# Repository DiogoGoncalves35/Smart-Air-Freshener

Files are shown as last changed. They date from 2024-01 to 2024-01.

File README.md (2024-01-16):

# Smart Air Freshner

    

This board is designed to control a standard Air Freshener via ESPHome and Home Assistant, this way it's possible to automate the device by time or any condition defined.





The board fits in the same place as the default board because both have the same dimensions.





------------

### Schematic 

The [schematic](/Hardware/PCB/Schematic.pdf) is arround ESP12-E module with the basic configuration (Resistors needed), the AMS1117 regulates the 5V input voltage to 3.3V. The microcontroller controls the motor via an 2N2222 transistor and the 1N4007 diode protects the circuit in case of back voltage generated when the motor turns off.

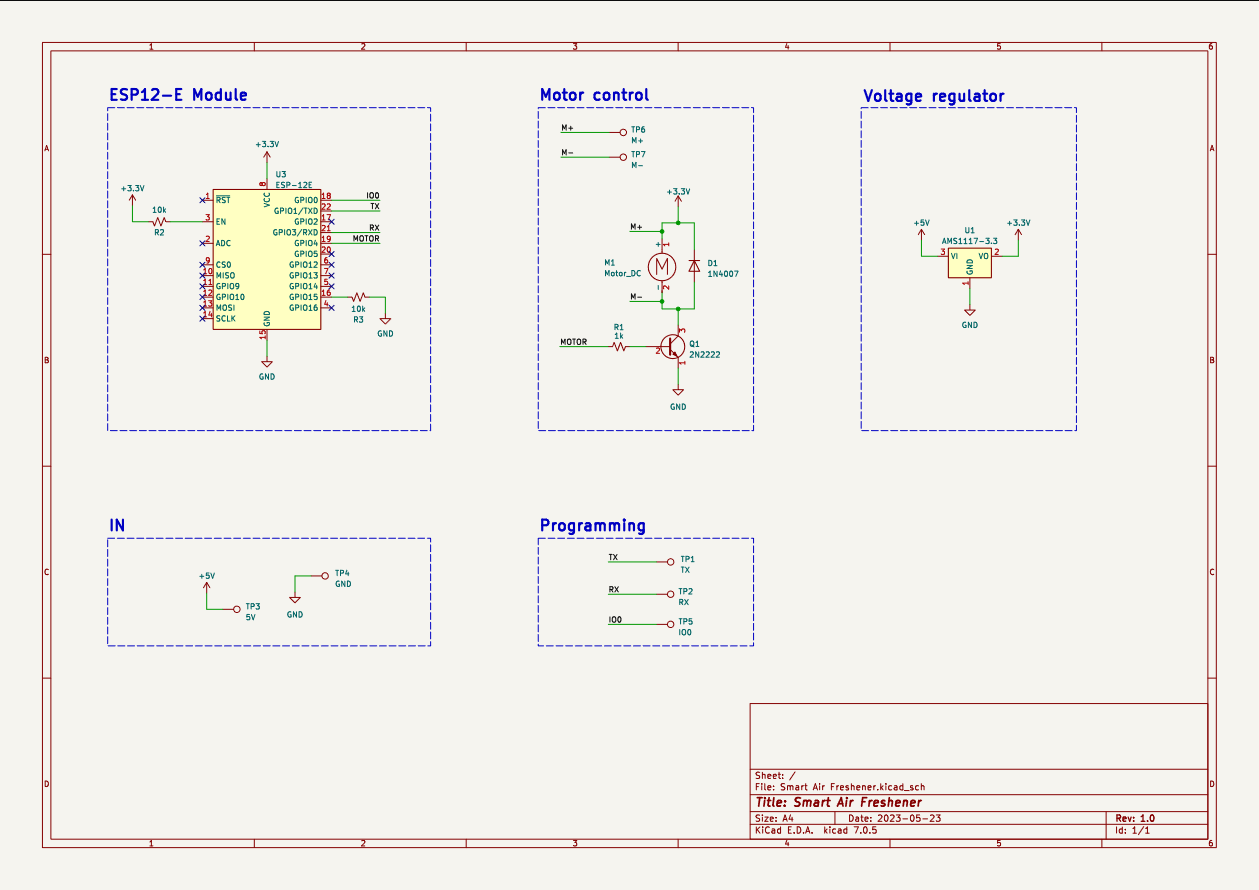
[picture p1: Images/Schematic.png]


------------

### PCB

[This](Hardware/PCB/) 1.6mm board contains 2 layers, both connected to GND, under the antenna GND area was removed. Programming connectors are SMD because it's only necessary to program the board once, after, it's possible to program over-the-air. Design it's not the best and should be improved, the only problem is related to component placement, there isn't much space to put the components on the edges.

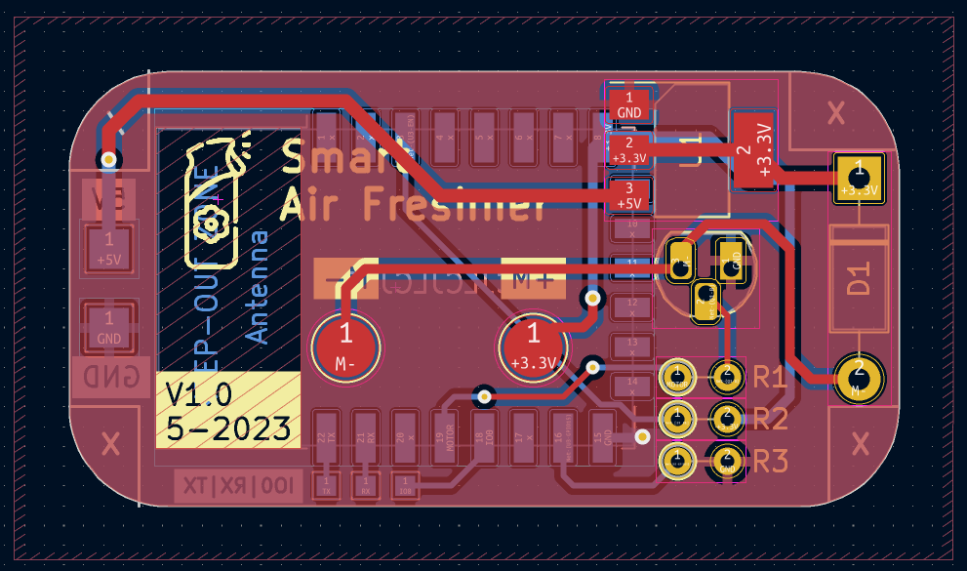
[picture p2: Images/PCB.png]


---

### ESPHome Code

This code block contains the needed code to control the air freshener. Whenever Spray button is pressed in Home Assistant, the motor turns on for a second and then turns off. With the button inside HA, it's possible to automate the device in different ways.

```
button:
  - platform: template
    name: "Spray"
    icon: "mdi:air-purifier"
    on_press:
    - switch.turn_on: motor
    - delay: 1000ms
    - switch.turn_off: motor

switch:
  - platform: gpio
    pin: GPIO4
    id: motor
```
------------

### Known issues

- None for now

------------

### To-Do

- USB-C connector ? (Better for connecting, removes need for soldering)
- Fuse protection
- SMD components

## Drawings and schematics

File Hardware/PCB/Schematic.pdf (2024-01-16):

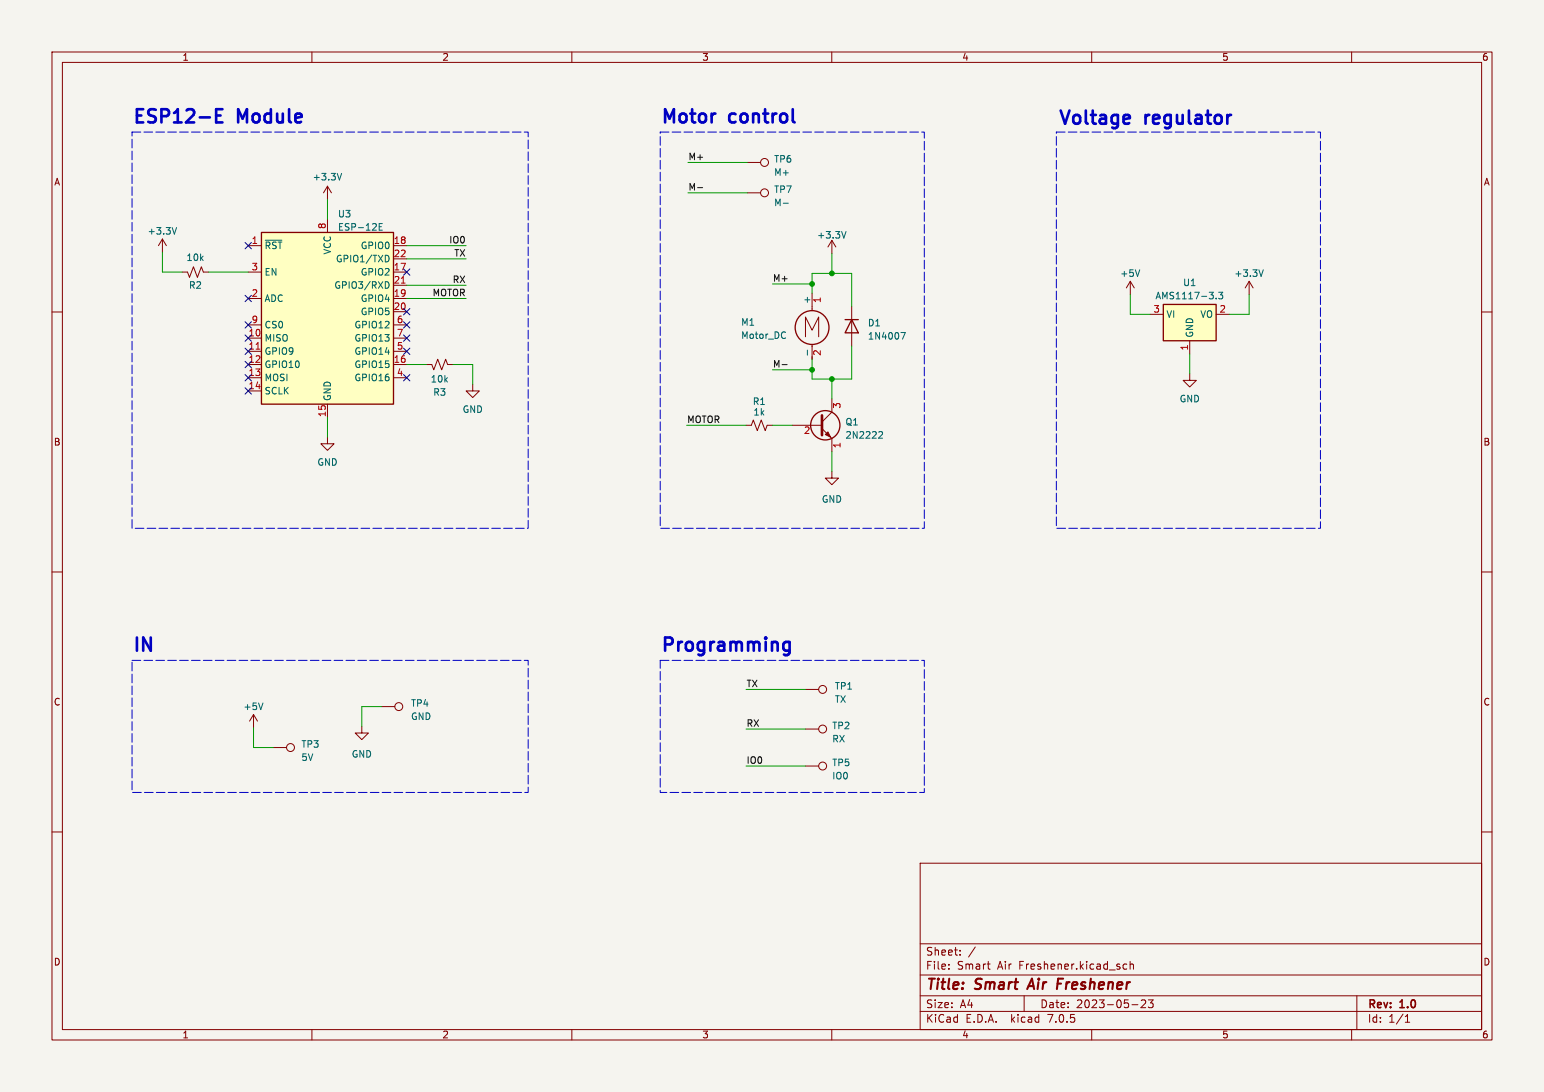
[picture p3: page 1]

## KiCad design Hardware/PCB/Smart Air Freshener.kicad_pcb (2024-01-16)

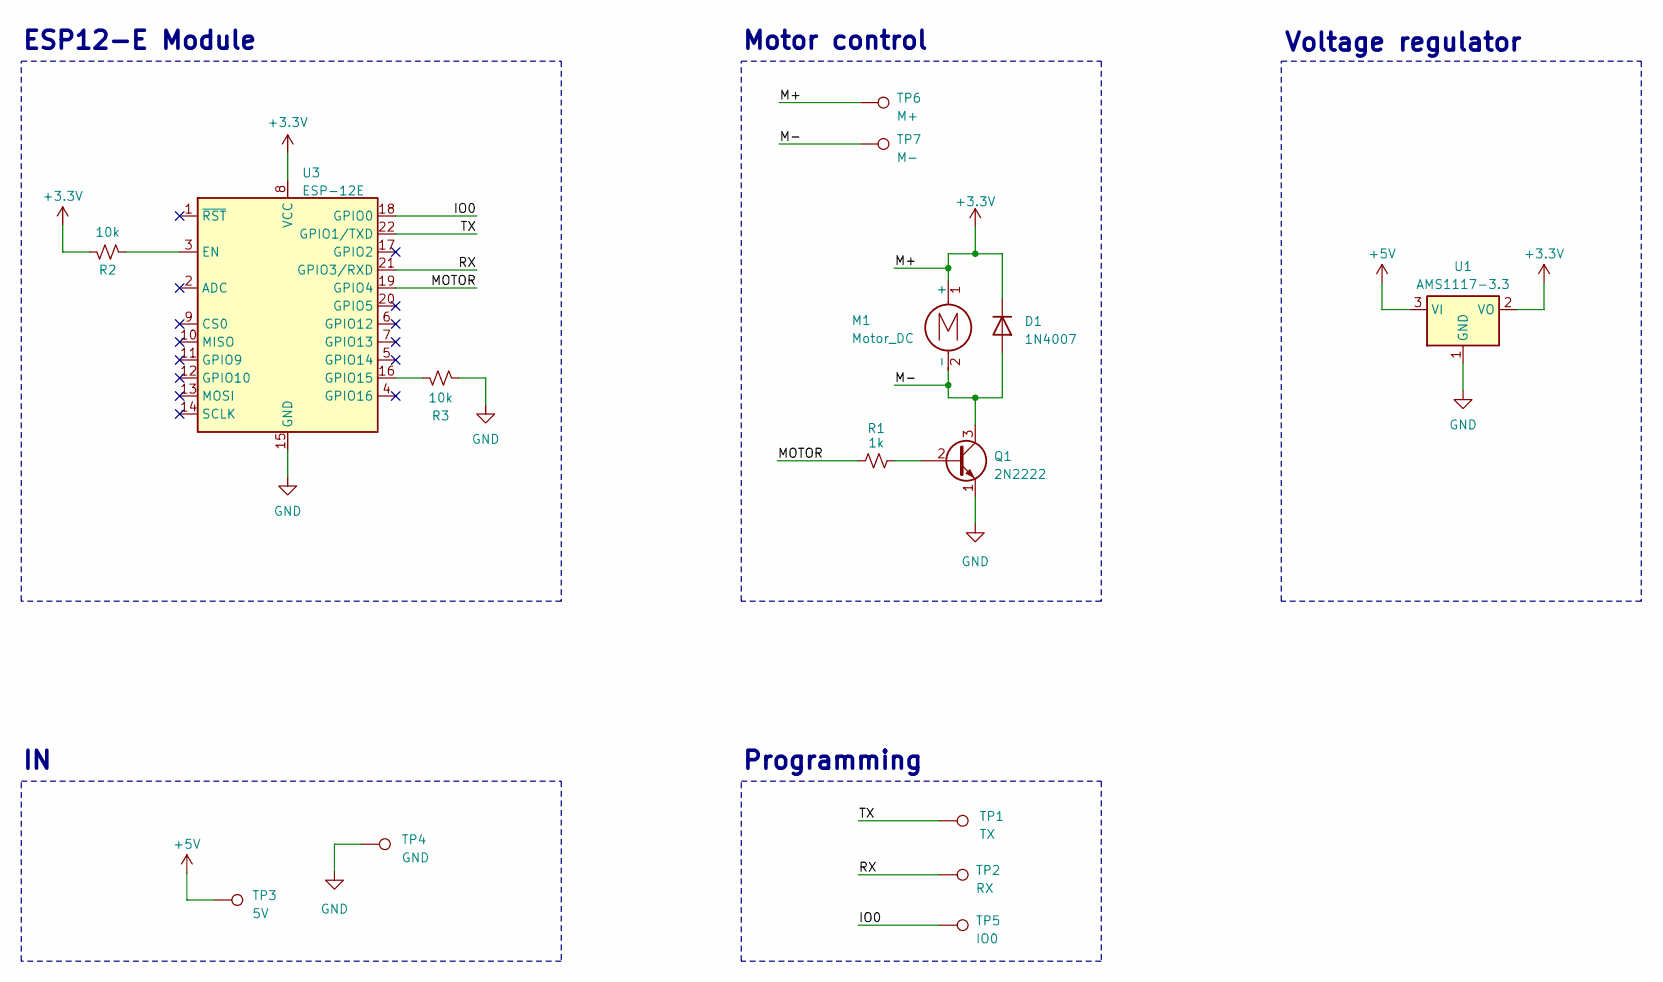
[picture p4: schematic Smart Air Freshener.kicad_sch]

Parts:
D1: 1N4007; D_DO-41_SOD81_P10.16mm_Horizontal
M1: Motor_DC
Q1: 2N2222; TO-92_HandSolder
R1: 1k; R_Axial_DIN0204_L3.6mm_D1.6mm_P2.54mm_Vertical
R2, R3: 10k; R_Axial_DIN0204_L3.6mm_D1.6mm_P2.54mm_Vertical; LCSC C25804
TP1: TX; TestPoint_Pad_1.0x1.0mm
TP2: RX; TestPoint_Pad_1.0x1.0mm
TP3: 5V; TestPoint_Pad_2.0x2.0mm
TP4: GND; TestPoint_Pad_2.0x2.0mm
TP5: IO0; TestPoint_Pad_1.0x1.0mm
TP6: M+; TestPoint_Pad_D3.0mm
TP7: M-; TestPoint_Pad_D3.0mm
U1: AMS1117-3.3; SOT-223-3_TabPin2
U3: ESP-12E

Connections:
+3.3V: D1.1 (K), M1.1 (+), R2.2, TP6.1, U1.2 (VO), U3.8 (VCC)
+5V: TP3.1, U1.3 (VI)
/IO0: TP5.1, U3.18 (GPIO0)
/M-: D1.2 (A), M1.2 (-), Q1.3 (C), TP7.1
/MOTOR: R1.1, U3.19 (GPIO4)
/RX: TP2.1, U3.21 (GPIO3/RXD)
/TX: TP1.1, U3.22 (GPIO1/TXD)
GND: Q1.1 (E), R3.2, TP4.1, U1.1 (GND), U3.15 (GND)
unnamed: Q1.2 (B), R1.2
unnamed: R2.1, U3.3 (EN)
unnamed: R3.1, U3.16 (GPIO15)

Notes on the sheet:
Voltage regulator
ESP12-E Module
Motor control
Programming

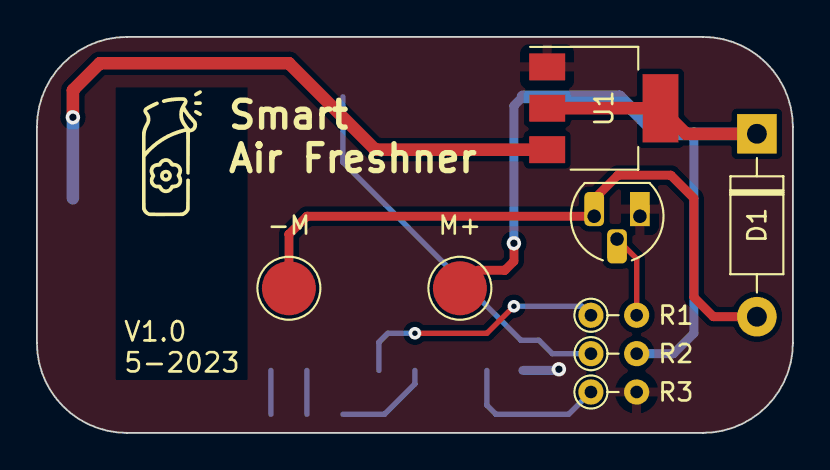
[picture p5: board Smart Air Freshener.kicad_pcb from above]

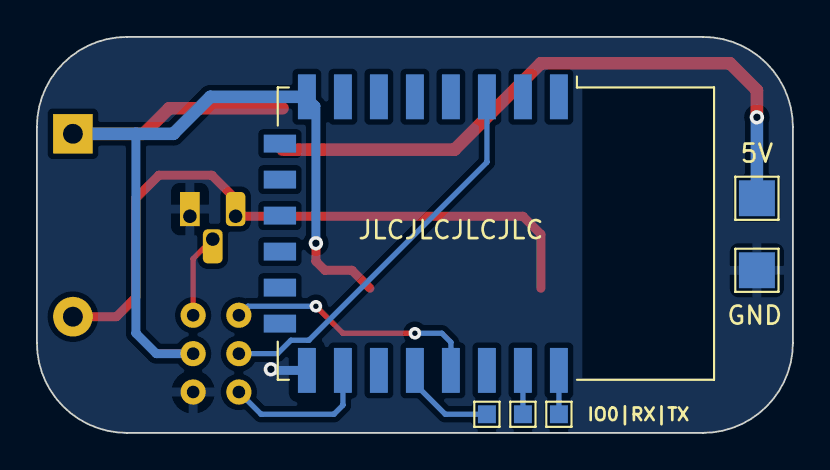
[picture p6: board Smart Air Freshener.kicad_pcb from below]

Board: 2 copper layers, 42.0 x 22.0 mm, 14 parts (6 on the bottom side), 11 nets.
